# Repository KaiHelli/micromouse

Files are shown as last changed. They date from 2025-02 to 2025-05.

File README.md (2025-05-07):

# Micromouse

An autonomous micromouse designed and built at the Technical University of Munich (TUM) to explore and solve a 6×6 full-size maze and find its center. This project was done as part of the master practical course *Micromouse: Designing an Educational Racing-Robot from Scratch* under supervision of Dr. Alexander Lenz.

This mouse was built by the group of: Jázmin, Paulo, Ágnes, and Kai.

## Table of Contents

- [Micromouse](#micromouse)
  - [Table of Contents](#table-of-contents)
  - [Features](#features)
  - [Repository Structure](#repository-structure)
  - [Hardware Design](#hardware-design)
  - [Software Architecture](#software-architecture)

## Features

- **Hardware**  
  - dsPIC33FJ64MC804 microcontroller  
  - GP2Y0A51 analog distance sensors (front, left, right)  
  - ICM-20948 9-axis IMU for orientation
  - Toshiba TB6612FNG H-Bridge with Faulhaber DC motors  
  - 64×32 OLED display for real-time maze mapping  
  - RN4871 Bluetooth LE module & UART for data streaming  
  - Piezo buzzer (RTTTL melodies)  
  - 7.4 V battery input with 5 V/3.3 V linear regulators  
- **Firmware**  
  - UART & I²C drivers (sync/async)
  - OLED graphics library (SSD1306)
  - Timers & external interrupts with callback registration  
  - Odometry (encoders + gyro + distance sensors)  
  - Positional PD controller with feed-forward & side-wall PI  
  - Trapezoidal velocity profiles for straight & turning motions  
  - Flood-fill navigation with exploration & optimized final run  
- **Scripts**  
  - Python scripts for sensor calibration, feed-forward gain fitting, velocity profiling, and plotting  
  - Data analysis & visualization scripts and CSV data 

## Repository Structure

```
.
├── 3d/         # 3D-printed part designs (Autodesk Fusion) -> TODO: Add files
├── data/       # Raw & processed data logs
│ ├── *.csv
│ └── processed/
├── img/        # Figures/plots from experiments
├── imu_cal/    # IMU calibration scripts & data
├── logo/       # Team and TUM logos
├── pcb/        # Eagle files, design rule files & BOMs
├── scripts/    # Python tools for calibration & plotting
├── src/        # Embedded firmware source & build files
│ ├── adc.c/.h, i2c.c/.h, imu.c/.h, …
│ └── Makefile # Build configuration for MPLAB/xc16
└── README.md
```

## Hardware Design

1. **Schematic & PCB**  
   - Eagle files under `pcb/` (schematics, board, design rules, footprints).  
   - ADC decoupling / low-pass filter, star-shaped power rails, and IMU in center
2. **Sensors & Peripherals**  
   - Distance sensors: analog voltage → distance polynomial fit
   - IMU: offline accel/mag ellipsoid fit + gyro bias calibration on startup.  
   - OLED: SSD1306 over I²C for maze display.  
3. **Mechanical**  
   - Motor & sensor mounts (3D-printed; see `3d/`).  
   - Battery holder below PCB for low center of gravity.  

## Software Architecture

- **Configuration**
  - `src/constants.h`
  - `src/IOconfig.h/.c`
- **Drivers**  
  - `src/dma.c`, `src/clock.c`, `src/adc.c`, `src/uart.c`, `src/i2c.c`, `src/timers.c`, `src/pwm.c`, `src/switches.c`, `src/ssd1306.c`, …
- **Applications**  
  - `src/globalTimers.c` – provides a microsecond-resolution system timer running since power-up.  
  - `src/mazeSolver.c` – implements the flood-fill algorithm for exploration and the optimized run to the maze center.  
  - `src/oled.c` – manages the SSD1306 display’s frame buffer, draws the maze and updates only the regions that change.  
  - `src/rtttl.c` – decodes RTTTL ringtone strings and drives the piezo buzzer to play melodies.  
  - `src/imu.c` – interfaces with the 9-axis IMU over I²C, applies calibration, and reads gyro/accel/mag data.  
  - `src/sensor.s` – reads raw ADC values from the distance sensors and converts them into calibrated distance measurements.  
  - `src/motors.c` – controls the motor driver to set each wheel’s speed as a percentage of maximum.  
  - `src/motorEncoders.c` – reads quadrature encoder counts and uses a PLL to estimate wheel angular velocity.  
- **Control**  
  - `src/mouseController.c` – implements positional PD control with feed-forward terms for precise trajectory tracking  
  - `src/move.c` – generates trapezoidal velocity profiles for both linear and rotational movements  
- **Utilities**  
  - `src/data_visualizer/*.dvws` for creating interactive plots in MPLAB’s Data Visualizer  
- **Unused**
  - `src/odometry.c` – abandoned sensor-fusion odometry module, superseded by integrated controller-based estimation.

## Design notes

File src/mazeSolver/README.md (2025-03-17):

# Maze Traversal using Flood Fill
v1.0

## PID Control 
First implementation in demo project
```c
/*
 *         _
 *   /\/\ (_) ___ _ __ ___  _ __ ___   ___  _   _ ___  ___
 *  /    \| |/ __| '__/ _ \| '_ ` _ \ / _ \| | | / __|/ _ \
 * / /\/\ \ | (__| | | (_) | | | | | | (_) | |_| \__ \  __/
 * \/    \/_|\___|_|  \___/|_| |_| |_|\___/ \__,_|___/\___|
 *
 * Example program to showcase the Micromouse API for the demo mouse.
 *
 * File:   main.c
 *
 */

#include "UART.h"
#include "boot.h"
#include "configBits.h"
#include "encoders.h"
#include "globalTimer.h"
#include "leds.h"
#include "motors.h"
#include "sensors.h"
#include "switches.h"
#include "timers.h"

#include <stdio.h>
#include <xc.h>

/* EXAMPLE FUNCTIONS */

/**
 * Routine to toggle LED1 using a timer. This functions signature matches the TimerCallback typedef from the timers.h file.
 * @return 1 to keep the timer running, if 0 is returned the timer will stop
 */
int toggle_led1(void)
{
    LED1 = !LED1;
    return 1; // return 1 to keep the timer running
}

/**
 * Routine to toggle LED2 using the button SW1. This functions signature matches the SwitchCallback typedef from the switches.h file.
 * Returns nothing.
 */
void toggle_led2(void)
{
    LED2 = !LED2;
}

/**
 * Routine to toggle LED3 using the UART RX interrupt. This functions signature matches the UARTCallback typedef from the UART.h file.
 */
void toggle_led3(unsigned int registerContent)
{
    LED3 = !LED3;
}

/**
 * Routine to toggle LED4 using the UART TX interrupt. This functions signature matches the UARTCallback typedef from the UART.h file.
 */
void toggle_led4(unsigned int registerContent)
{
    LED4 = !LED4;
}

/**
 * Routine to stream sensor readings over UART. This can be used to visualize the sensor readings in MPLAB Data Visualizer.
 *
 * Workspace file "sensor_test.dvws" can be found in this directory to setup the correct variable streamer.
 *
 * See MPLAB X Visualizer documentation for the protocol: MPLABÂ® Data Visualizer User's Guide (DS50003001) - 5.2 Stream Format
 */
int stream_sensor_data(void)
{
    LED1 = !LED1;
    UART_TXint8(FRAME_MARKER); // start of visualizer frame
    UART_TXint8(sensors_readFront());
    UART_TXint8(sensors_readLeft());
    UART_TXint8(sensors_readRight());
    UART_TXUInt(sensors_readFrontRaw());
    UART_TXUInt(sensors_readLeftRaw());
    UART_TXUInt(sensors_readRightRaw());
    UART_TXLong(encoders_getAngleLeftDegrees());
    UART_TXLong(encoders_getAngleRightDegrees());
    UART_TXFloat(encoders_getAngleLeftRadians());
    UART_TXFloat(encoders_getAngleRightRadians());
    UART_TXFloat(encoders_getRPMLeft());
    UART_TXFloat(encoders_getRPMRight());
    UART_TXFloat(encoders_getRadPerSecLeft());
    UART_TXFloat(encoders_getRadPerSecRight());
    UART_TXLong(encoders_getTicksLeft());
    UART_TXLong(encoders_getTicksRight());
    UART_TXint8(~FRAME_MARKER); // end of visualizer frame (one's complement of start marker)
    return 1;                   // return 1 to keep the timer running
}

/* Prints the current time since boot in ms to UART, formatted in ASCII */
int transmit_time(void)
{
    char timestring[20];
    sprintf(timestring, "Time: %lu\n", globalTimer_getTimeInUS() / 1000); // devide by 1000 to convert to ms
    UART_TXString(timestring);
    return 1;
}

/**
 * Routine to toggle the motors using the button SW1. This functions signature matches the SwitchCallback typedef from the switches.h file.
 */
void toggle_motors(void)
{
    static int running = 0;
    if (running)
    {
        motors_setMotorLeft(0);
        motors_setMotorRight(0);
        running = 0;
    }
    else
    {
        motors_setMotorLeft(0.3);
        motors_setMotorRight(0.3);
        running = 1;
    }
}

struct PID{
    float K_p;
    float K_i;
    float K_d;
    float last_error;
    //output
    float w_l;
    float w_r;
    float w_f;
};

//PID struct
struct PID pid_state;

//state 
static int started = 0;

void init_PID(struct PID* pid) {
    pid->K_p = 0.0007;
    pid->K_i = 0;
    pid->K_d = 0.0001;
    pid->last_error = 0;
    pid->w_l = 0;
    pid->w_r = 0;
    pid->w_f = 0;
}

void update_PID(struct PID* pid, uint8_t left, uint8_t right, uint8_t front) {
    //TODO set w_f according to front distance
    float error = (float)(left - right);
    pid->w_l = pid->w_f - pid->K_p * error - pid->K_d * (error - pid->last_error);
    pid->w_r = pid->w_f + pid->K_p * error + pid->K_d * (error - pid->last_error);
    if(pid->w_l > 1) pid->w_l = 1.0;
    if(pid->w_r > 1) pid->w_r = 1.0;
    if(pid->w_l < -1) pid->w_l = -1.0;
    if(pid->w_r < -1) pid->w_r = -1.0;
    pid->last_error = error;
}

void toggle_control() {
    
    //initialize PID
    init_PID(&pid_state);
    
    if (started)
    {
        motors_setMotorLeft(0);
        motors_setMotorRight(0);
        started = 0;
    }
    else
    {   
        pid_state.w_f = 0.35;
        started = 1;
    } 
}

/* Prints the current time since boot in ms to UART, formatted in ASCII */
int update_control(void)
{   
    if (started) {
        uint8_t left = sensors_readLeft();
        uint8_t right = sensors_readRight();
        uint8_t front = sensors_readFront();
        update_PID(&pid_state, left, right, front);
        motors_setMotorLeft(pid_state.w_l);
        motors_setMotorRight(pid_state.w_r);
    }
    return 1;
}

/* MAIN FUNCTION */

int main() {
    
    LED1 = LEDOFF;
    LED2 = LEDOFF;
    LED3 = LEDOFF;
    LED4 = LEDOFF;

    // initializes the peripherals, must be called first
    boot_setup();

    // initializes the UART1 module with a baud rate of 115200
    UART_setup(115200);

    // Example timer usage
    timers_initTimerInMS(1, 419);
    timers_registerTimerCallback(1, &update_control);
    timers_startTimer(1);

    // test switches
    switches_registerSW1Callback(&toggle_control);

    // infinite loop
    while (1) {}
    return 0;
}

int main1()
{   
    //PID struct
    struct PID pid;
    
    LED1 = LEDOFF;
    LED2 = LEDOFF;
    LED3 = LEDOFF;
    LED4 = LEDOFF;

    // initializes the peripherals, must be called first
    boot_setup();

    // initializes the UART1 module with a baud rate of 115200
    UART_setup(115200);

    //initialize PID
    init_PID(&pid);
    
    // Example timer usage
    timers_initTimerInMS(1, 419);
    timers_registerTimerCallback(1, &transmit_time);
    timers_startTimer(1);

    // test switches
    switches_registerSW1Callback(&toggle_motors);

    // test UART callbacks
    UART_registerRX1Callback(&toggle_led3);
    UART_registerTX1Callback(&toggle_led4);

    // infinite loop
    while (1) {}
    return 0;
}
```

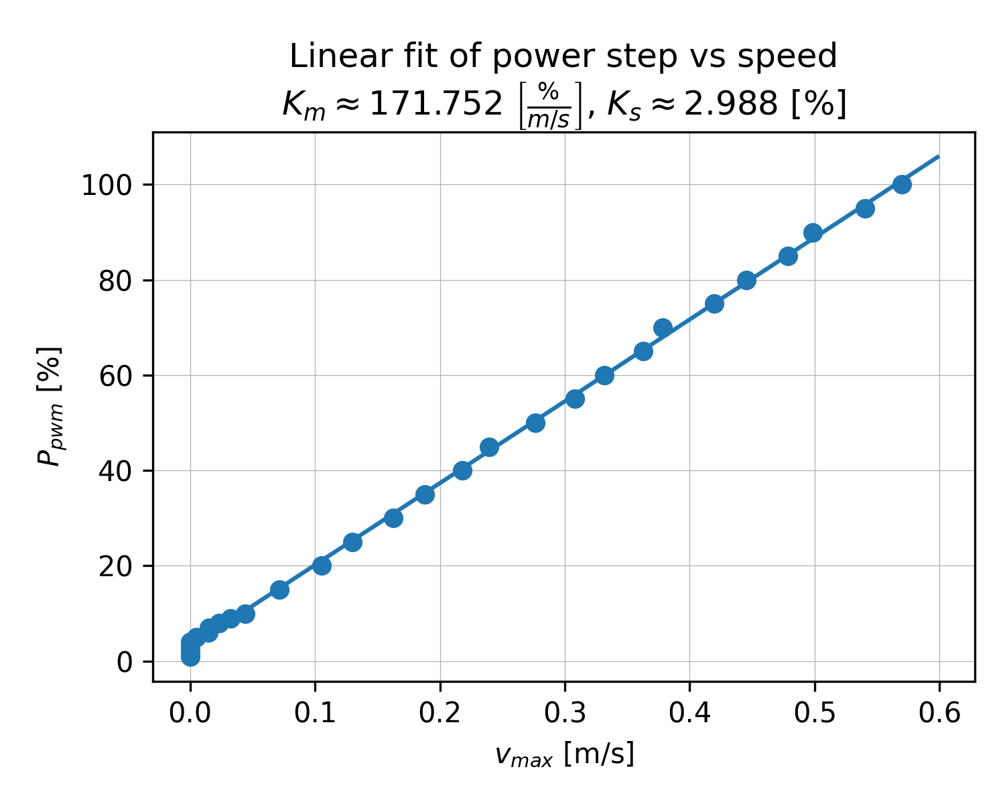
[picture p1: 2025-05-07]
img/vmax_fit_linear.png

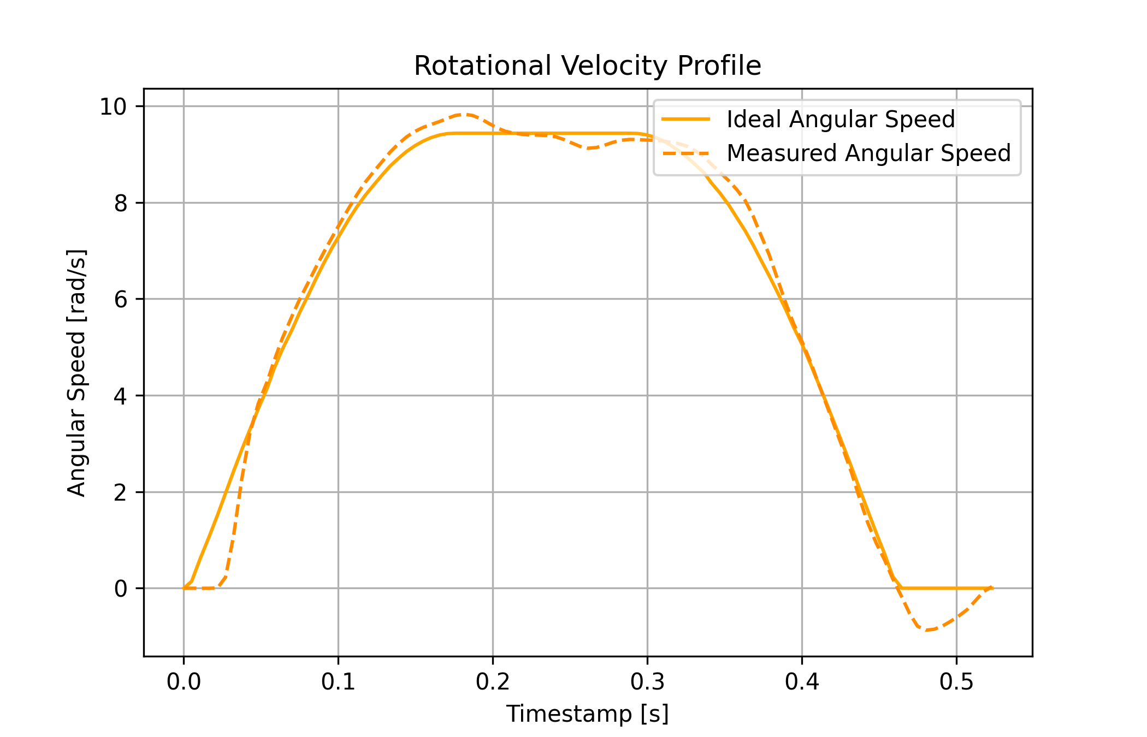
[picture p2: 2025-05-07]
img/vel_profile_angular.png

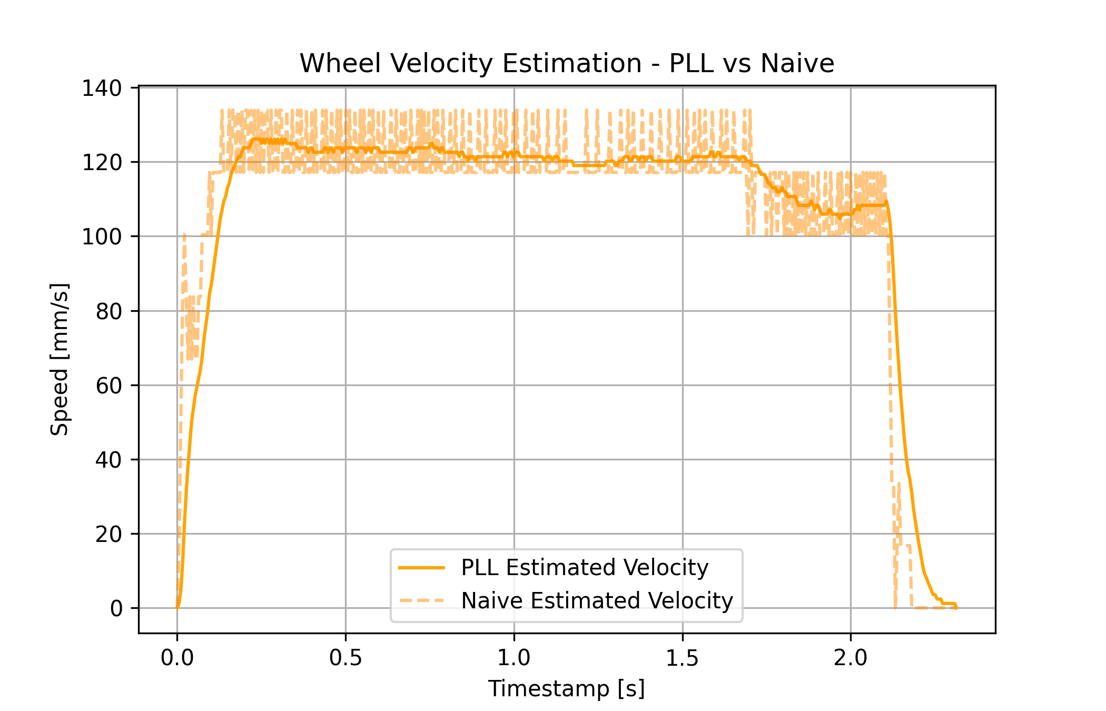
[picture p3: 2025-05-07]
img/enc_velocities_comparison.png

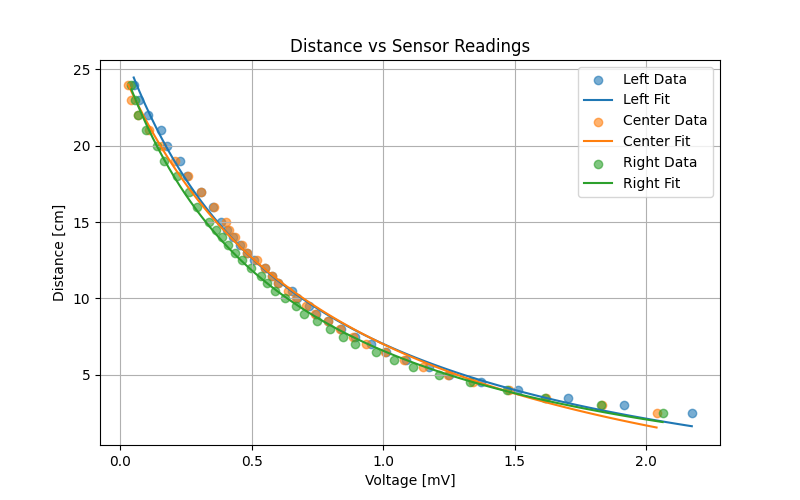
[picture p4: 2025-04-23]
img/distance_fast_sensor_fit.png

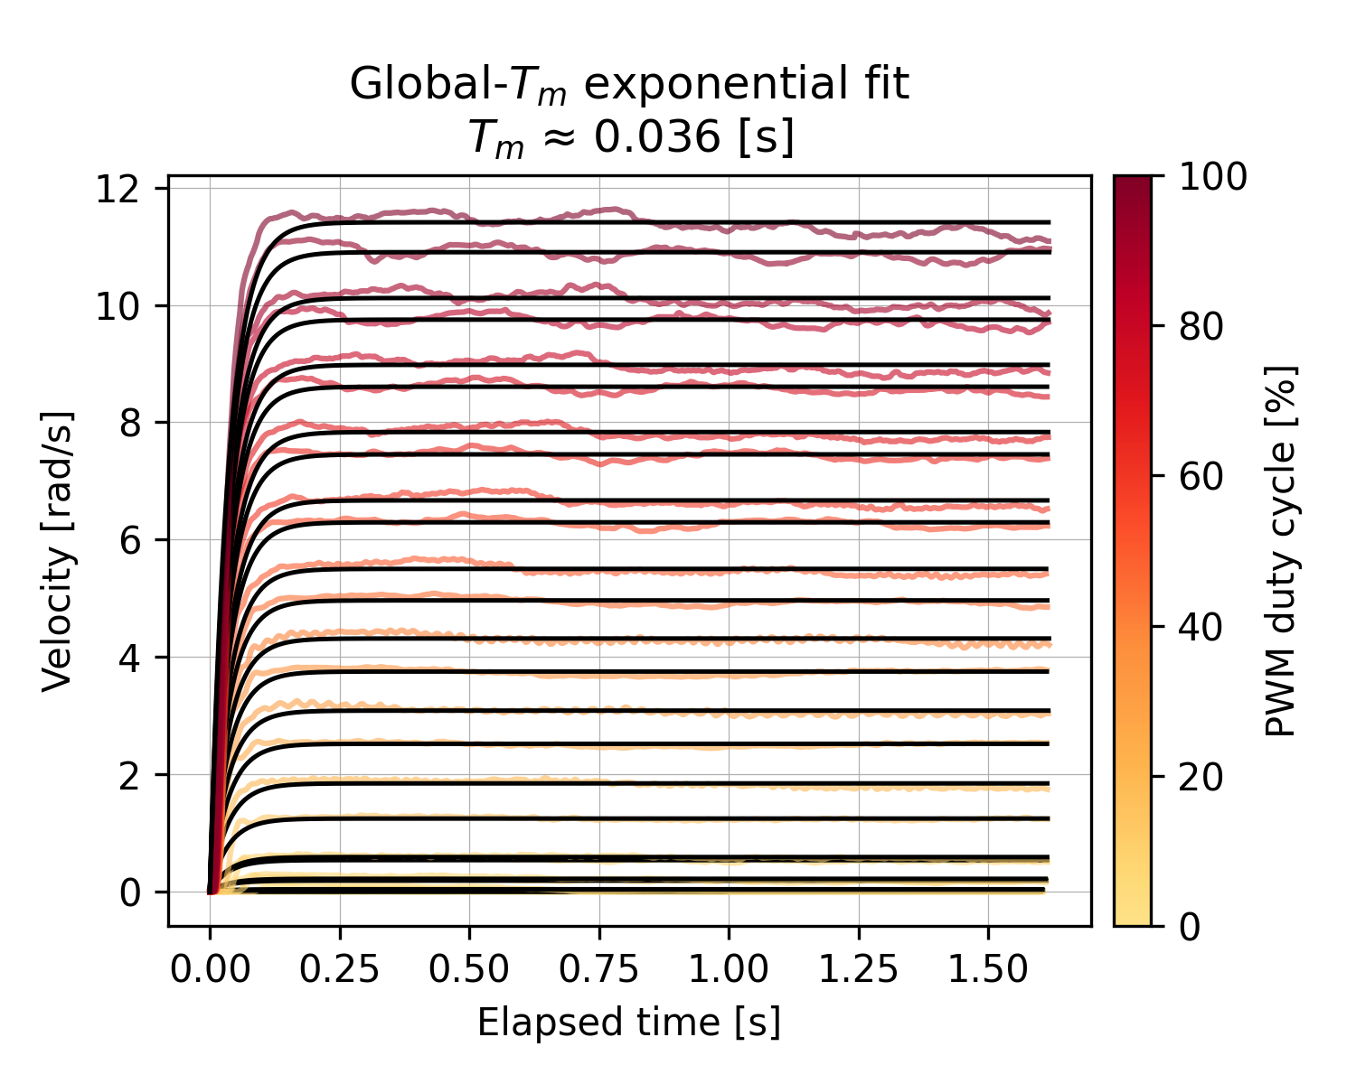
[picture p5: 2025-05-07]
img/Tm_fit_angular.png

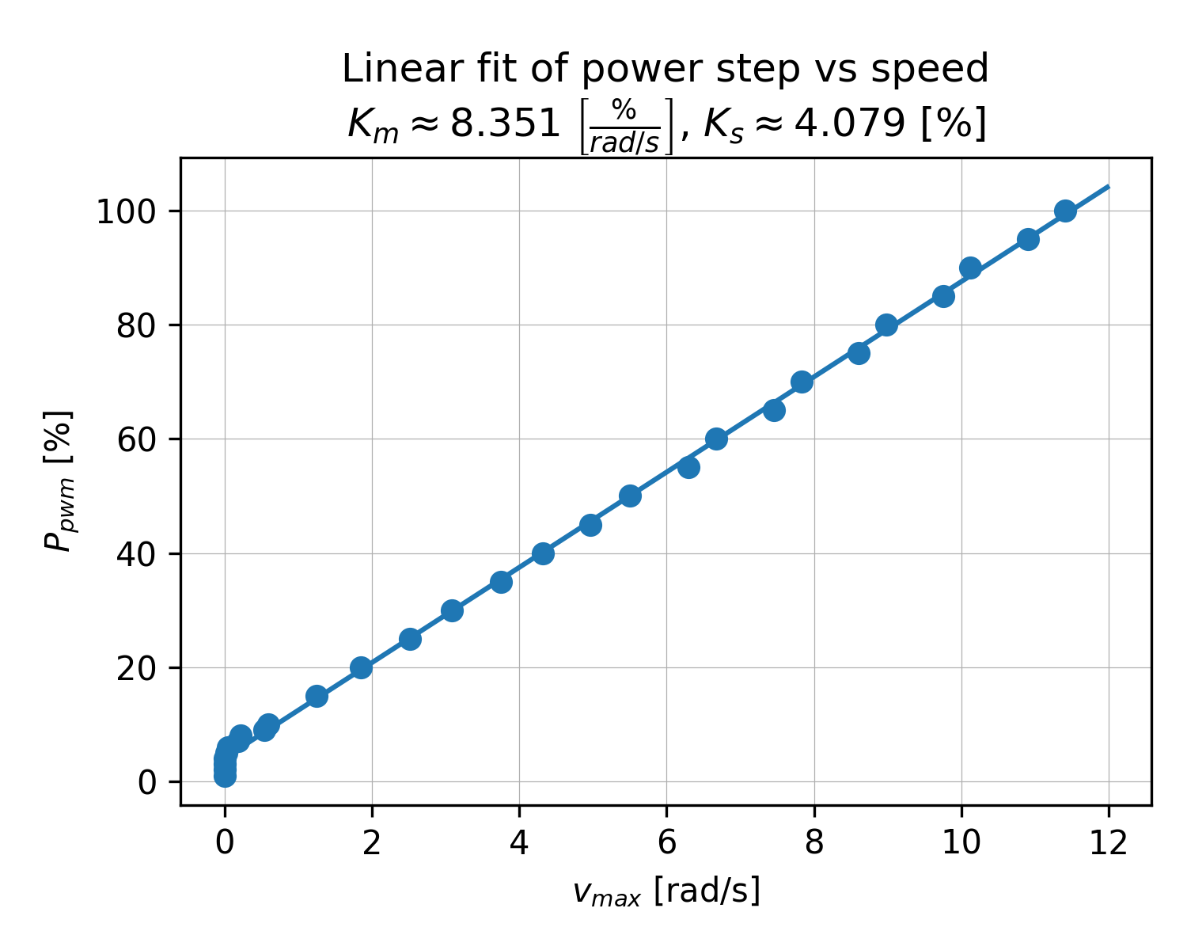
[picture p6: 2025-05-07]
img/vmax_fit_angular.png

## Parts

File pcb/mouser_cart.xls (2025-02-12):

WARENKORB
Dies ist keine Rechnung
11-Feb-25 18:27:51
 | Mouser-Nr. | Herst.- Nr. | Hersteller | Kunden-Teilenr | Beschreibung | RoHS | Lebenszyklus | Stückzahl | Preis (EUR) | Gesamtpreis: (EUR)
1 | 579-RN4871-I/RM140 | RN4871-I/RM140 | Microchip |  | Bluetooth-Module – 802.15.1 Bluetooth Low Energy BLE Module, Shielded, Antenna, ASCII Interface, 9x11.5mm | RoHS-konform |  | 1 | 8,78 € | 8,78 €
2 | 667-ERJ-PB6B1001V | ERJ-PB6B1001V | Panasonic |  | Dickfilmwiderstände - SMD 0805 Anti-Surge Res. 0.1%, 1Kohm | RoHS: Konform durch Ausnahmegenehmigung |  | 6 | 0,276 € | 1,66 €
3 | 771-PMEG4010ER115 | PMEG4010ER,115 | Nexperia |  | Schottky Dioden & Gleichrichter PMEG4010ER/SOD123W/SOD2 | RoHS: Konform durch Ausnahmegenehmigung |  | 1 | 0,20 € | 0,20 €
4 | 667-ERJ-PB6B2201V | ERJ-PB6B2201V | Panasonic |  | Dickfilmwiderstände - SMD 0805 Anti-Surge Res. 0.1%, 2.2Kohm | RoHS: Konform durch Ausnahmegenehmigung |  | 2 | 0,276 € | 0,55 €
5 | 667-ERJ-PB6B2701V | ERJ-PB6B2701V | Panasonic |  | Dickfilmwiderstände - SMD 0805 Anti-Surge Res. 0.1%, 2.7Kohm | RoHS: Konform durch Ausnahmegenehmigung |  | 1 | 0,323 € | 0,32 €
6 | 604-APT2012LZGCK | APT2012LZGCK | Kingbright |  | Einfarbige LEDs leds 2.0X1.2MM LOW CRNT | RoHS-konform |  | 3 | 0,513 € | 1,54 €
7 | 604-APT2012LVBCD | APT2012LVBC/D | Kingbright |  | Einfarbige LEDs leds 2.0X1.2MM LOW CRNT | RoHS-konform |  | 1 | 0,513 € | 0,51 €
8 | 604-APT2012LSECKJ3RV | APT2012LSECK/J3-PRV | Kingbright |  | Einfarbige LEDs leds 2.0X1.2MM LOW CRNT | RoHS-konform |  | 5 | 0,58 € | 2,90 €
9 | 179-TS046650BK100SMR | TS04-66-50-BK-100-SMT-TR | Same Sky |  | Sensorschalter 6 x 6 mm 5 mm Actuator Height 100 gf Black Surface Mount TR SPST Tactile | RoHS-konform | Neues Produkt | 2 | 0,181 € | 0,36 €
10 | 611-1101M2S3CQE2 | 1101M2S3CQE2 | C&K Switches |  | Schiebeschalter SP ON-NONE-ON PTH AG | RoHS-konform |  | 1 | 5,13 € | 5,13 €
11 | 151-302-RC | 151-302-RC | Kobiconn |  | Prüfstecker und Messbuchsen LONG YEL PCB TERM | RoHS-konform |  | 4 | 0,443 € | 1,77 €
12 | 571-1761681-1 | 1761681-1 | TE Connectivity |  | Sockel & Kabelgehäuse IDC LOW PRO HDR 6P VERT HT BLACK | RoHS-konform |  | 2 | 1,18 € | 2,36 €
13 | 81-LQH43PN470M26L | LQH43PN470M26L | Murata |  | Leistungsinduktivitäten – SMD 47 UH 20% | RoHS-konform |  | 1 | 0,466 € | 0,47 €
14 | 179-CPT-9019A-SMT-TR | CPT-9019A-SMT-TR | Same Sky |  | Lautsprecher u. Umformer 9.0 mm square 1.9 mm deep P 4.0 kHz 3 V SMT no driving circuit T&R package A | RoHS-konform | Neues Produkt | 1 | 0,836 € | 0,84 €
15 | 774-ATS16A-E | ATS16A-E | CTS |  | Quarze 16MHz 20pF 30ppm -40C 85C | RoHS-konform |  | 1 | 0,504 € | 0,50 €
16 | 485-4554 | 4554 | Adafruit |  | Entwicklungstools für multifunktionale Sensoren Adafruit TDK InvenSense ICM-20948 9-DoF IMU (MPU-9250 Upgrade) - STEMMA QT / Qwiic | RoHS-konform |  | 1 | 14,20 € | 14,20 €
17 | 852-GP2Y0A51SK0F | GP2Y0A51SK0F | Sharp Microelectronics |  | Entfernungssensor-Module - umschlossen | RoHS: Konform durch Ausnahmegenehmigung |  | 3 | 5,82 € | 17,46 €
18 | 757-TB6612FNGC8EL | TB6612FNG,C,8,EL | Toshiba |  | Motor / Bewegung / Zündungscontroller und Treiber Brush Motor Driver IC | RoHS-konform |  | 1 | 2,60 € | 2,60 €
19 | 926-LM1117DTX50NOPB | LM1117DTX-5.0/NOPB | Texas Instruments |  | LDO Spannungs-Regulator 800mA LDO Linear Reg A 926-LM1117DT50NOPB | RoHS-konform |  | 1 | 1,41 € | 1,41 €
20 | 926-LM1117DTX3.3NOPB | LM1117DTX-3.3/NOPB | Texas Instruments |  | LDO Spannungs-Regulator 800MA LDO LINEAR REG A 926-LM1117DT-3.3NOPB | RoHS-konform |  | 1 | 1,22 € | 1,22 €
21 | 579-DSPIC364MC804IPT | DSPIC33FJ64MC804-I/PT | Microchip |  | Digitale Signalprozessoren und Controller - DSP, DSC 16B DSC 64KB | RoHS-konform |  | 1 | 6,89 € | 6,89 €
22 | 667-ERJ-PB6B1002V | ERJ-PB6B1002V | Panasonic |  | Dickfilmwiderstände - SMD 0805 Anti-Surge Res. 0.1%, 10Kohm | RoHS: Konform durch Ausnahmegenehmigung |  | 4 | 0,276 € | 1,10 €
23 | 667-ERJ-PB6B5600V | ERJ-PB6B5600V | Panasonic |  | Dickfilmwiderstände - SMD 0805 Anti-Surge Res. 0.1%, 560ohm | RoHS: Konform durch Ausnahmegenehmigung |  | 2 | 0,257 € | 0,51 €
24 | 667-ERJ-PB6B1501V | ERJ-PB6B1501V | Panasonic |  | Dickfilmwiderstände - SMD 0805 Anti-Surge Res. 0.1%, 1.5Kohm | RoHS: Konform durch Ausnahmegenehmigung |  | 1 | 0,352 € | 0,35 €
25 | 710-61300211121 | 61300211121 | Wurth Elektronik |  | Sockel & Kabelgehäuse WR-PHD 2.54mm 2Pin T HT Header | RoHS-konform |  | 3 | 0,124 € | 0,37 €
26 | 710-61300311121 | 61300311121 | Wurth Elektronik |  | Sockel & Kabelgehäuse WR-PHD 2.54mm Hdr 3P Single Str Gold | RoHS-konform |  | 2 | 0,124 € | 0,25 €
27 | 710-61300411121 | 61300411121 | Wurth Elektronik |  | Sockel & Kabelgehäuse WR-PHD 2.54mm Hdr 4P Single Str Gold | RoHS-konform |  | 1 | 0,181 € | 0,18 €
28 | 710-61300611121 | 61300611121 | Wurth Elektronik |  | Sockel & Kabelgehäuse WR-PHD 2.54mm 6Pin T HT Header | RoHS-konform |  | 1 | 0,333 € | 0,33 €
29 | 710-61300411821 | 61300411821 | Wurth Elektronik |  | Sockel & Kabelgehäuse WR-PHD 2.54mm Scket Header 4 pins | RoHS-konform |  | 1 | 0,418 € | 0,42 €
30 | 710-61300611821 | 61300611821 | Wurth Elektronik |  | Sockel & Kabelgehäuse WR-PHD 2.54mm Socket Header 6 pins | RoHS-konform |  | 2 | 0,342 € | 0,68 €
31 | 710-61304011821 | 61304011821 | Wurth Elektronik |  | Platine-zu-Platine & Mezzanine-Steckverbinder WR-PHD 2.54 mm Socket Header 40P 1Row straight gold plating | RoHS-konform | Neu bei Mouser | 1 | 2,77 € | 2,77 €
32 | 710-61304011121 | 61304011121 | Wurth Elektronik |  | Sockel & Kabelgehäuse WR-PHD 2.54mm Hdr 40 P Single Str Gold | RoHS-konform |  | 1 | 1,45 € | 1,45 €
33 | 80-C0805C200J5GAUTO | C0805C200J5GACAUTO | KEMET |  | Kondensator aus mehreren Keramikschichten MLCC - SMD/SMT 50V 20pF C0G 0805 5% AEC-Q200 | RoHS-konform |  | 2 | 0,209 € | 0,42 €
34 | 80-C0805C104K4JAUTO | C0805C104K4JACAUTO | KEMET |  | Kondensator aus mehreren Keramikschichten MLCC - SMD/SMT Cap Cer 0805 0.1F 16VDC U2J | RoHS-konform |  | 8 | 0,57 € | 4,56 €
35 | 80-C0805C105J3RECAUT | C0805C105J3RECAUTO | KEMET |  | Kondensator aus mehreren Keramikschichten MLCC - SMD/SMT 25V 1uF X7R 0805 5% AEC-Q200 | RoHS-konform |  | 4 | 0,266 € | 1,06 €
36 | 80-C0805C106K4P | C0805C106K4PACTU | KEMET |  | Kondensator aus mehreren Keramikschichten MLCC - SMD/SMT 16V 10uF X5R 0805 10% | RoHS-konform |  | 6 | 0,162 € | 0,97 €
37 | 581-TAJP106K010RNJ | TAJP106K010RNJ | KYOCERA AVX |  | Tantalkondensatoren - fest für SMD 10V 10uF 10% | RoHS-konform |  | 3 | 0,542 € | 1,63 €
38 | 581-TLJR226M010R3800 | TLJR226M010R3800 | KYOCERA AVX |  | Tantalkondensatoren - fest für SMD 10V 22uF 20% ESR=380 0 | RoHS-konform |  | 2 | 0,656 € | 1,31 €
39 | 863-NTR1P02T1G | NTR1P02T1G | onsemi |  | MOSFETs -20V -1A P-Channel | RoHS-konform |  | 1 | 0,323 € | 0,32 €
Durch das Absenden Ihrer Bestellung erklären Sie sich mit diesen Geschäftsbedingungen einverstanden. (https://www.mouser.de/saleterms) |  |  |  |  |  |  |  |  | Ware: | 90,35 €
Die Preise sind zum angezeigten Datum und zur Uhrzeit reflektiert. |  |  |  |  |  |  |  |  | Versandkosten: | 0,00 €

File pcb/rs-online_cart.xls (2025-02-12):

RS Stock No | Quantity | Cost Centre | Description | Manufacturer Part. No. | Manufacturer name | Unit Price | Total Price
1805375 | 10 |  | RS PRO Stecker Leistungssteckverbinder, Stecker, 2P, Gold, 45A, 500 V dc | XT60PW-M | RS PRO | 1455 | 1455
2256195 | 1 |  | Midas 0.49Zoll OLED-Display 64 x 32pixels, 11.18 x 5.58mm Weiß Passiv-Matrix, I2C Interface | MDOB064032AV-WI | Midas | 673 | 673
8201649 | 20 |  | JST ZH Vorverdrahtete Crimp-Kontakte verzinnt 0.05mm², 300mm | 01SZHSZH-30L-300 | JST | 444 | 888
8201646 | 10 |  | JST ZH Steckverbindergehäuse Buchse 1.5mm, 3-polig / 1-reihig Gerade, Kabelmontage für Trennbarer Crimp-Steckverbinder | ZHR-3 | JST | 6 | 6

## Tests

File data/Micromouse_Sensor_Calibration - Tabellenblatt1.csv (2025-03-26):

Abstand [cm] | Left [/1000 V] | Center [/1000 V] | Right [/1000 V]
1 | 3170 | 3098 | 3107
1,5 | 2891 | 2662 | 2730
2 | 2481 | 2369 | 2354
2,5 | 2173 | 2039 | 2062
3 | 1917 | 1830 | 1828
3,5 | 1702 | 1617 | 1615
4 | 1514 | 1477 | 1472
4,5 | 1373 | 1342 | 1330
5 | 1252 | 1246 | 1213
5,5 | 1174 | 1151 | 1112
6 | 1085 | 1080 | 1042
6,5 | 1010 | 1008 | 971
7 | 952 | 934 | 894
7,5 | 892 | 886 | 846
8 | 840 | 836 | 797
8,5 | 792 | 789 | 749
9 | 744 | 742 | 700
9,5 | 719 | 707 | 670
10 | 671 | 670 | 626
10,5 | 652 | 639 | 589
11 | 602 | 602 | 560
11,5 | 578 | 576 | 537
12 | 552 | 551 | 498
12,5 | 510 | 522 | 463
13 | 484 | 481 | 437
13,5 | 455 | 463 | 412
14 | 430 | 438 | 388
14,5 | 406 | 413 | 364
15 | 382 | 403 | 338
16 | 354 | 357 | 293
17 | 307 | 309 | 264
18 | 255 | 259 | 216
19 | 229 | 208 | 166
20 | 180 | 158 | 139
21 | 155 | 111 | 100
22 | 106 | 67 | 70
23 | 71 | 42 | 56
24 | 52 | 31 | 43
25 | 36 | 23 | 33
30 | 22 | 23 | 22

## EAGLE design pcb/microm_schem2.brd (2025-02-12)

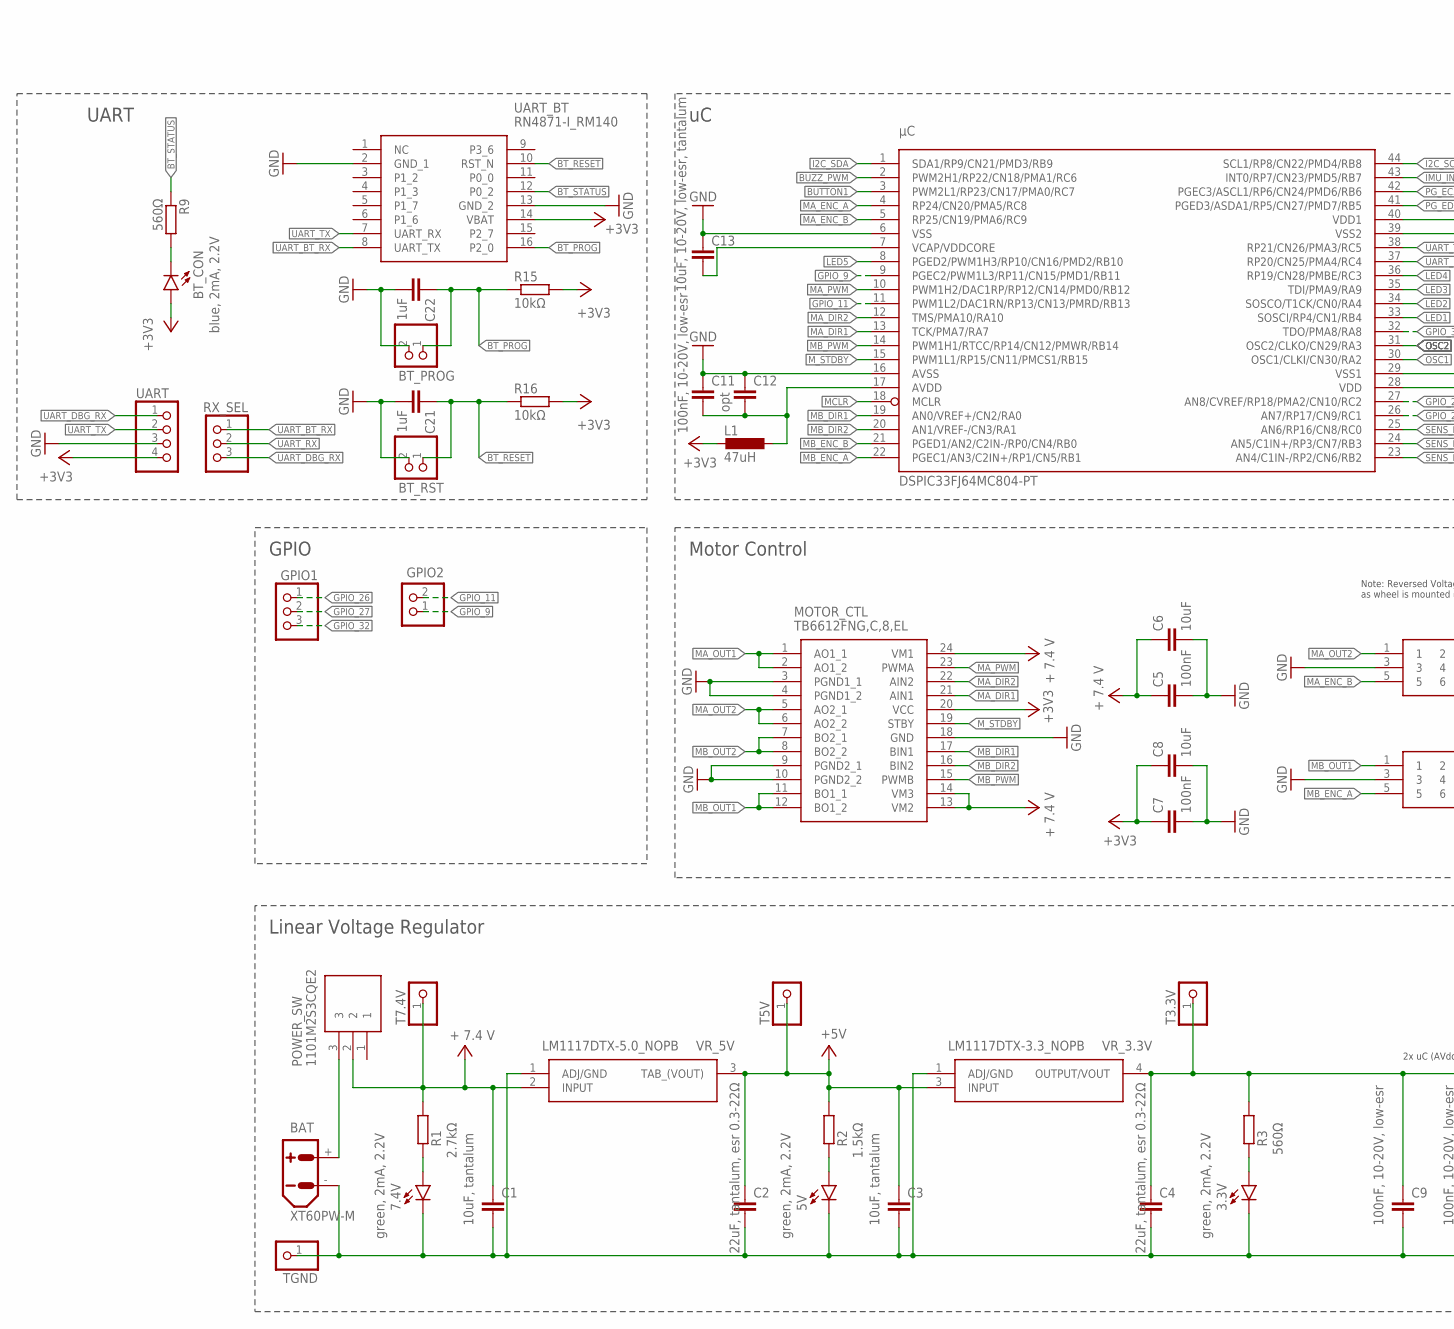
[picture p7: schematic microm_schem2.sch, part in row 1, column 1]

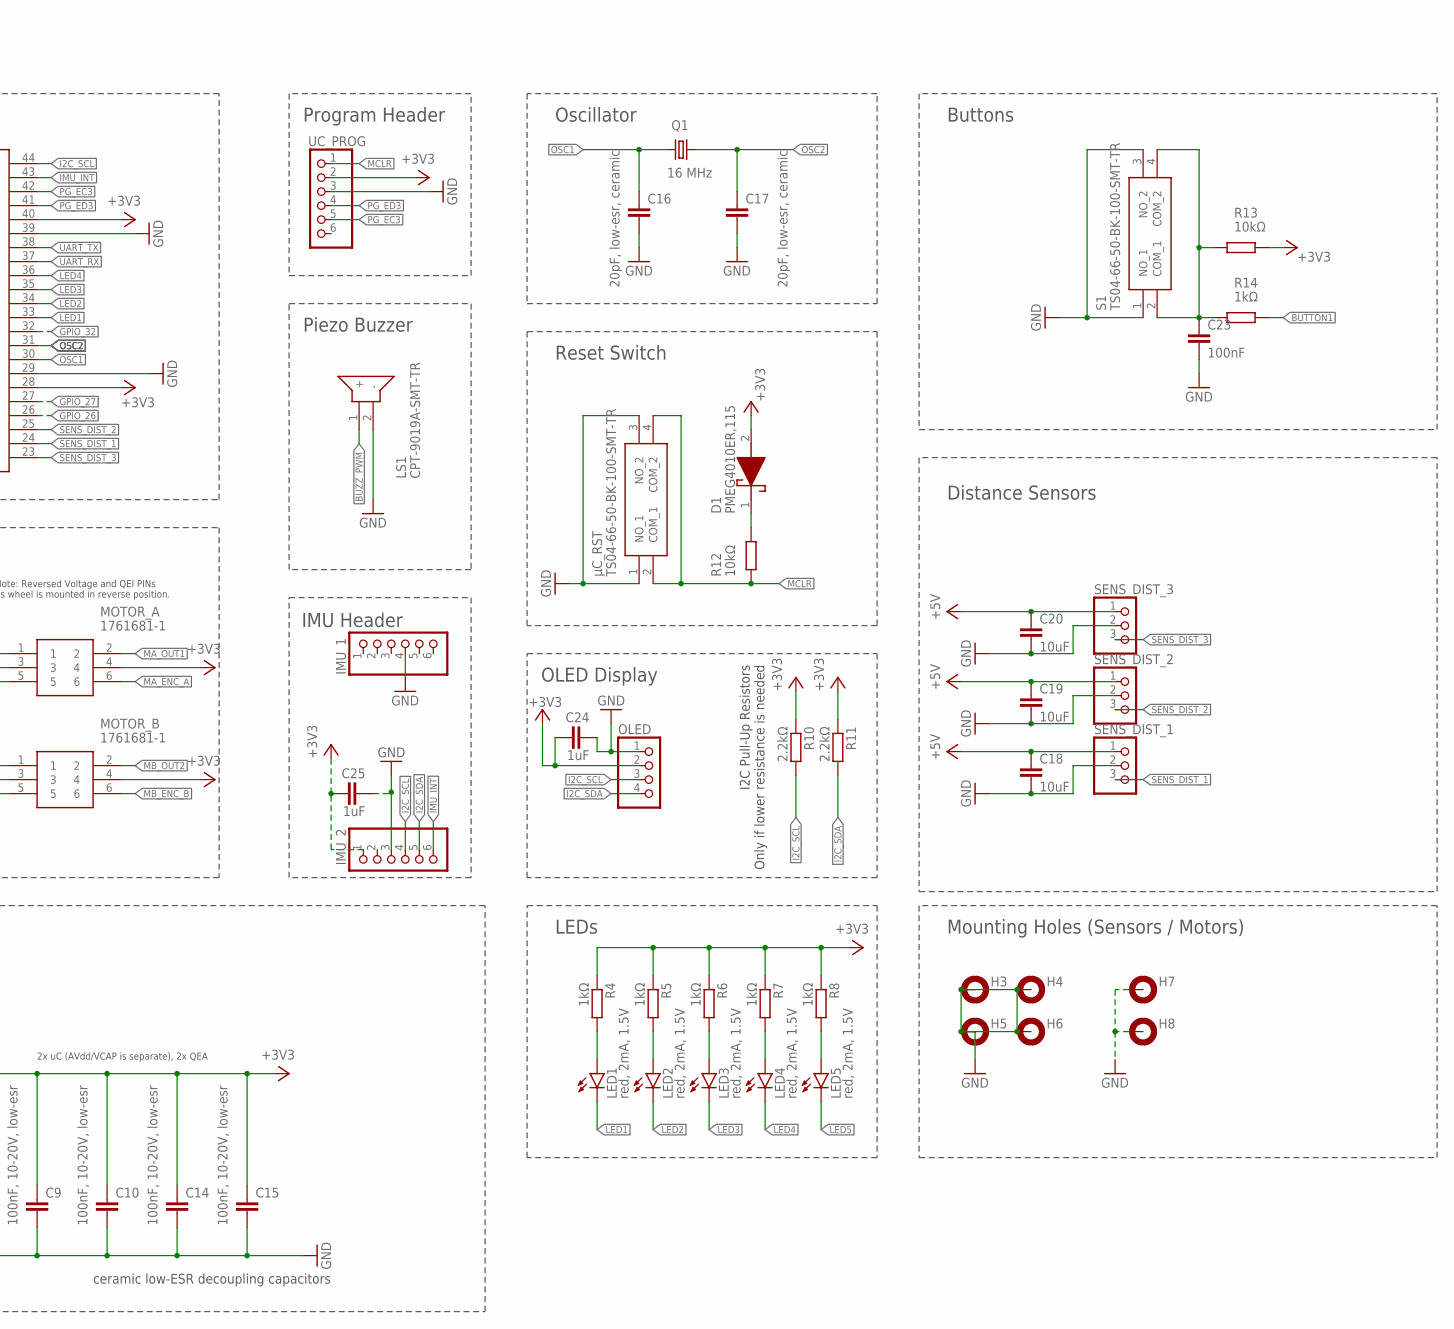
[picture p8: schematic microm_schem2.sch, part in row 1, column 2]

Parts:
3.3V, 5V, 7.4V: green, 2mA, 2.2V; CHIP-LED0805
BAT: XT60PW-M
BT_CON: blue, 2mA, 2.2V; CHIP-LED0805
BT_PROG: PINHD-1X2; 1X02
BT_RST: PINHD-1X2; 1X02
C1, C3: 10uF, tantalum; C0805
C2, C4: 22uF, tantalum, esr 0.3-22Ω; C0805
C5, C7, C23: 100nF; C0805
C6, C8, C18, C19, C20: 10uF; C0805
C9, C10, C11, C14, C15: 100nF, 10-20V, low-esr; C0805
C12: opt; C0805
C13: 10uF, 10-20V, low-esr, tantalum; C0805
C16, C17: 20pF, low-esr, ceramic; C0805
C21, C22, C24, C25: 1uF; C0805
D1: PMEG4010ER,115; PMEG4010ER115
GPIO1: PINHD-1X3; 1X03
GPIO2: PINHD-1X2; 1X02
H3, H4, H5, H6, H7, H8: MOUNT-PAD-ROUND2.8; 2,8-PAD
IMU_1, IMU_2: PINHD-1X6; 1X06
L1: 47uH; L1812
LED1, LED2, LED3, LED4, LED5: red, 2mA, 1.5V; CHIPLED_0805
LS1: CPT-9019A-SMT-TR; CPT9019ASMTTR
MOTOR_A: 1761681-1; SHDR6W67P254_2X3_1524X916X922P
MOTOR_B: 1761681-1; SHDR6W67P254_2X3_1524X916X922P
MOTOR_CTL: TB6612FNG,C,8,EL; SOP65P760X160-24N
OLED: PINHD-1X4; 1X04
POWER_SW: 1101M2S3CQE2; 1000-SERIES(SPDT)
Q1: 16 MHz; HC49/S
R1: 2.7kΩ; R0805
R2: 1.5kΩ; R0805
R3, R9: 560Ω; R0805
R4, R5, R6, R7, R8, R14: 1kΩ; R0805
R10, R11: 2.2kΩ; R0805
R12, R13, R15, R16: 10kΩ; R0805
RX_SEL: PINHD-1X3; 1X03
S1: TS04-66-50-BK-100-SMT-TR; TS046650BK100SMTTR
SENS_DIST_1, SENS_DIST_2, SENS_DIST_3: PINHD-1X3; 1X03
T3.3V, T5V, T7.4V: PINHD-1X1; 1X01
TGND: PINHD-1X1; 1X01
UART: PINHD-1X4; 1X04
UART_BT: RN4871-I_RM140; RN4871IRM140
UC_PROG: PINHD-1X6; 1X06
VR_3.3V: LM1117DTX-3.3_NOPB; LM1117DTX33NOPB
VR_5V: LM1117DTX-5.0_NOPB; LM78M05CDT
µC_RST: TS04-66-50-BK-100-SMT-TR; TS046650BK100SMTTR
μC: DSPIC33FJ64MC804-PT; TQFP44

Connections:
+3V3: BT_CON.A, C4.1, C7.1, C8.1, C9.1, C10.1, C14.1, C15.1, C24.1, C25.1, D1.2 (A), IMU_2.1, L1.2, MOTOR_A.4, MOTOR_B.4, MOTOR_CTL.20 (VCC), OLED.2, R3.1, R4.1, R5.1, R6.1, R7.1, R8.1, R10.1, R11.1, R13.2, R15.2, R16.2, T3.3V.1, UART.4, UART_BT.14 (VBAT), UC_PROG.2, VR_3.3V.4 (OUTPUT/VOUT), μC.28 (VDD), μC.40 (VDD1)
+5V: C2.1, C3.1, C18.1, C19.1, C20.1, R2.1, SENS_DIST_1.1, SENS_DIST_2.1, SENS_DIST_3.1, T5V.1, VR_3.3V.3 (INPUT), VR_5V.3 (TAB_(VOUT))
+7V4: C1.1, C5.1, C6.1, MOTOR_CTL.13 (VM2), MOTOR_CTL.14 (VM3), MOTOR_CTL.24 (VM1), POWER_SW.2, R1.1, T7.4V.1, VR_5V.2 (INPUT)
BT_PROG: BT_PROG.1, C22.1, R15.1, UART_BT.16 (P2_0)
BT_RESET: BT_RST.1, C21.1, R16.1, UART_BT.10 (RST_N)
BT_STATUS: R9.1, UART_BT.12 (P0_2)
BUTTON1: R14.2, μC.3 (PWM2L1/RP23/CN17/PMA0/RC7)
BUZZ_PWM: LS1.1 (+), μC.2 (PWM2H1/RP22/CN18/PMA1/RC6)
GND: 3.3V.C, 5V.C, 7.4V.C, BAT.-, BT_PROG.2, BT_RST.2, C1.2, C2.2, C3.2, C4.2, C5.2, C6.2, C7.2, C8.2, C9.2, C10.2, C11.1, C12.1, C13.1, C14.2, C15.2, C16.2, C17.2, C18.2, C19.2, C20.2, C21.2, C22.2, C23.2, C24.2, C25.2, H3.B2,8, H4.B2,8, H5.B2,8, H6.B2,8, H7.B2,8, H8.B2,8, IMU_1.4, IMU_2.3, LS1.2 (-), MOTOR_A.3, MOTOR_B.3, MOTOR_CTL.3 (PGND1_1), MOTOR_CTL.4 (PGND1_2), MOTOR_CTL.9 (PGND2_1), MOTOR_CTL.10 (PGND2_2), MOTOR_CTL.18 (GND), OLED.1, S1.1 (NO_1), S1.3 (NO_2), SENS_DIST_1.2, SENS_DIST_2.2, SENS_DIST_3.2, TGND.1, UART.3, UART_BT.2 (GND_1), UART_BT.13 (GND_2), UC_PROG.3, VR_3.3V.1 (ADJ/GND), VR_5V.1 (ADJ/GND), µC_RST.1 (NO_1), µC_RST.3 (NO_2), μC.6 (VSS), μC.16 (AVSS), μC.29 (VSS1), μC.39 (VSS2)
GPIO_9: GPIO2.1, μC.9 (PGEC2/PWM1L3/RP11/CN15/PMD1/RB11)
GPIO_11: GPIO2.2, μC.11 (PWM1L2/DAC1RN/RP13/CN13/PMRD/RB13)
GPIO_26: GPIO1.1, μC.26 (AN7/RP17/CN9/RC1)
GPIO_27: GPIO1.2, μC.27 (AN8/CVREF/RP18/PMA2/CN10/RC2)
GPIO_32: GPIO1.3, μC.32 (TDO/PMA8/RA8)
I2C_SCL: IMU_2.4, OLED.3, R10.2, μC.44 (SCL1/RP8/CN22/PMD4/RB8)
I2C_SDA: IMU_2.5, OLED.4, R11.2, μC.1 (SDA1/RP9/CN21/PMD3/RB9)
IMU_INT: IMU_2.6, μC.43 (INT0/RP7/CN23/PMD5/RB7)
LED1: LED1.C, μC.33 (SOSCI/RP4/CN1/RB4)
LED2: LED2.C, μC.34 (SOSCO/T1CK/CN0/RA4)
LED3: LED3.C, μC.35 (TDI/PMA9/RA9)
LED4: LED4.C, μC.36 (RP19/CN28/PMBE/RC3)
LED5: LED5.C, μC.8 (PGED2/PWM1H3/RP10/CN16/PMD2/RB10)
MA_DIR1: MOTOR_CTL.21 (AIN1), μC.13 (TCK/PMA7/RA7)
MA_DIR2: MOTOR_CTL.22 (AIN2), μC.12 (TMS/PMA10/RA10)
MA_ENC_A: MOTOR_A.6, μC.4 (RP24/CN20/PMA5/RC8)
MA_ENC_B: MOTOR_A.5, μC.5 (RP25/CN19/PMA6/RC9)
MA_OUT1: MOTOR_A.2, MOTOR_CTL.1 (AO1_1), MOTOR_CTL.2 (AO1_2)
MA_OUT2: MOTOR_A.1, MOTOR_CTL.5 (AO2_1), MOTOR_CTL.6 (AO2_2)
MA_PWM: MOTOR_CTL.23 (PWMA), μC.10 (PWM1H2/DAC1RP/RP12/CN14/PMD0/RB12)
MB_DIR1: MOTOR_CTL.17 (BIN1), μC.19 (AN0/VREF+/CN2/RA0)
MB_DIR2: MOTOR_CTL.16 (BIN2), μC.20 (AN1/VREF-/CN3/RA1)
MB_ENC_A: MOTOR_B.5, μC.22 (PGEC1/AN3/C2IN+/RP1/CN5/RB1)
MB_ENC_B: MOTOR_B.6, μC.21 (PGED1/AN2/C2IN-/RP0/CN4/RB0)
MB_OUT1: MOTOR_B.1, MOTOR_CTL.11 (BO1_1), MOTOR_CTL.12 (BO1_2)
MB_OUT2: MOTOR_B.2, MOTOR_CTL.7 (BO2_1), MOTOR_CTL.8 (BO2_2)
MB_PWM: MOTOR_CTL.15 (PWMB), μC.14 (PWM1H1/RTCC/RP14/CN12/PMWR/RB14)
MCLR: R12.1, UC_PROG.1, µC_RST.2 (COM_1), µC_RST.4 (COM_2), μC.18 (MCLR)
M_STDBY: MOTOR_CTL.19 (STBY), μC.15 (PWM1L1/RP15/CN11/PMCS1/RB15)
unnamed: BT_CON.C, R9.2
unnamed: BAT.+, POWER_SW.3
unnamed: LED1.A, R4.2
unnamed: 7.4V.A, R1.2
unnamed: C11.2, C12.2, L1.1, μC.17 (AVDD)
unnamed: C23.1, R13.1, R14.1, S1.2 (COM_1), S1.4 (COM_2)
unnamed: D1.1 (K), R12.2
unnamed: LED2.A, R5.2
unnamed: 5V.A, R2.2
unnamed: 3.3V.A, R3.2
unnamed: LED3.A, R6.2
unnamed: LED4.A, R7.2
unnamed: LED5.A, R8.2
OSC1: C16.1, Q1.1, μC.30 (OSC1/CLKI/CN30/RA2)
OSC2: C17.1, Q1.2, μC.31 (OSC2/CLKO/CN29/RA3)
PG_EC3: UC_PROG.5, μC.42 (PGEC3/ASCL1/RP6/CN24/PMD6/RB6)
PG_ED3: UC_PROG.4, μC.41 (PGED3/ASDA1/RP5/CN27/PMD7/RB5)
SENS_DIST_1: SENS_DIST_1.3, μC.24 (AN5/C1IN+/RP3/CN7/RB3)
SENS_DIST_2: SENS_DIST_2.3, μC.25 (AN6/RP16/CN8/RC0)
SENS_DIST_3: SENS_DIST_3.3, μC.23 (AN4/C1IN-/RP2/CN6/RB2)
UART_BT_RX: RX_SEL.1, UART_BT.8 (UART_TX)
UART_DBG_RX: RX_SEL.3, UART.1
UART_RX: RX_SEL.2, μC.37 (RP20/CN25/PMA4/RC4)
UART_TX: UART.2, UART_BT.7 (UART_RX), μC.38 (RP21/CN26/PMA3/RC5)
VCAP/VDDCORE: C13.2, μC.7 (VCAP/VDDCORE)

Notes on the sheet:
Oscillator
Program Header
Reset Switch
Distance Sensors
Motor Control
ceramic low-ESR decoupling capacitors
Linear Voltage Regulator
LEDs
Buttons
Piezo Buzzer
IMU Header
UART
2x uC (AVdd/VCAP is separate), 2x QEA
Note: Reversed Voltage and QEI PINs as wheel is mounted in reverse position.
I2C Pull-Up Resistors Only if lower resistance is needed
Mounting Holes (Sensors / Motors)
OLED Display
GPIO

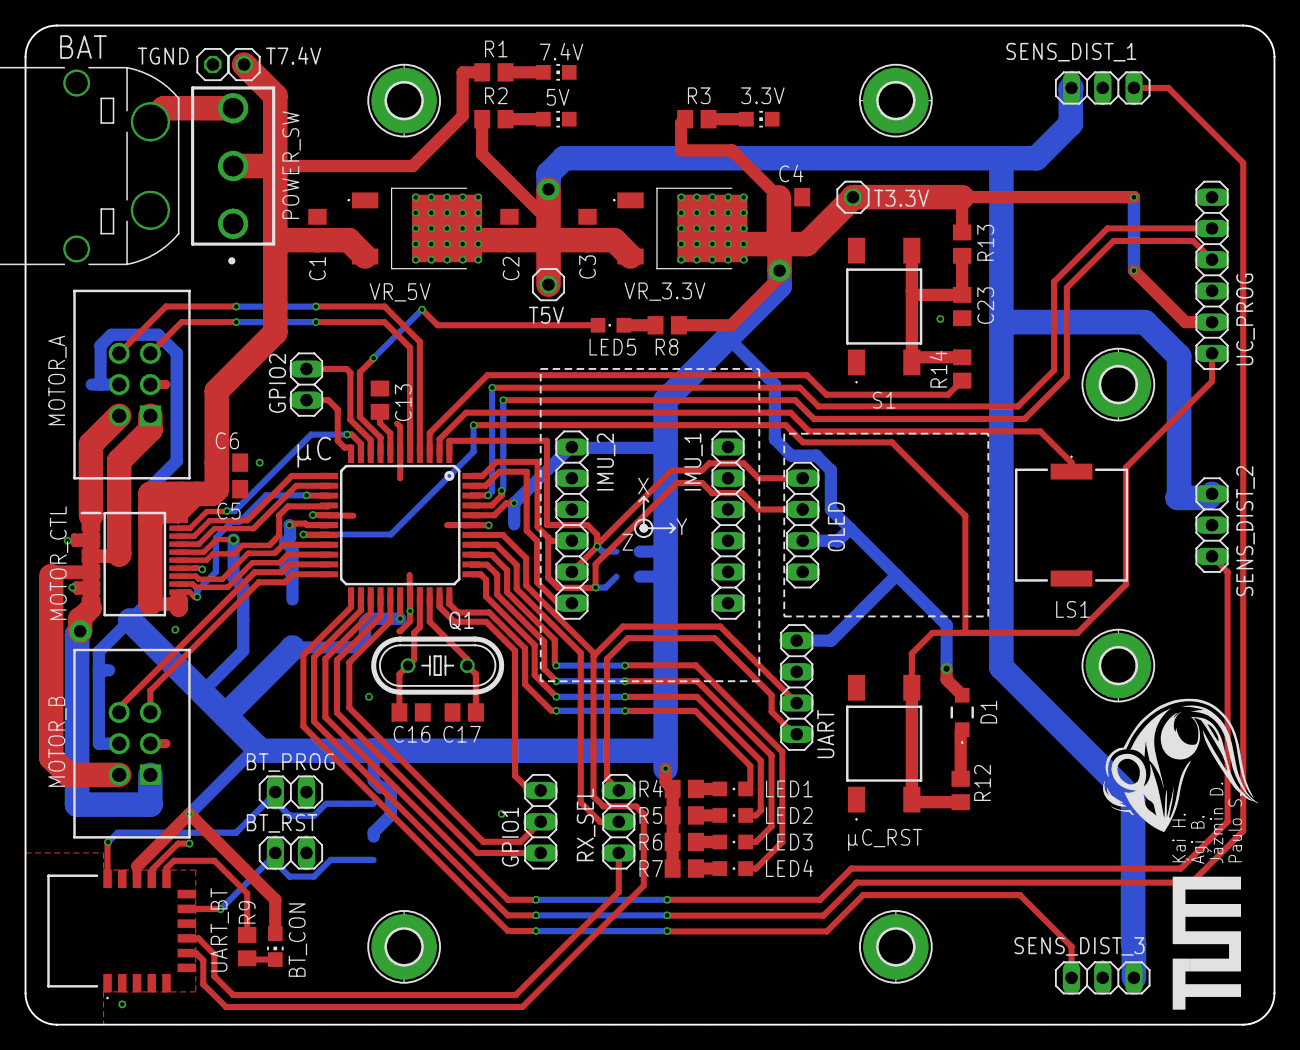
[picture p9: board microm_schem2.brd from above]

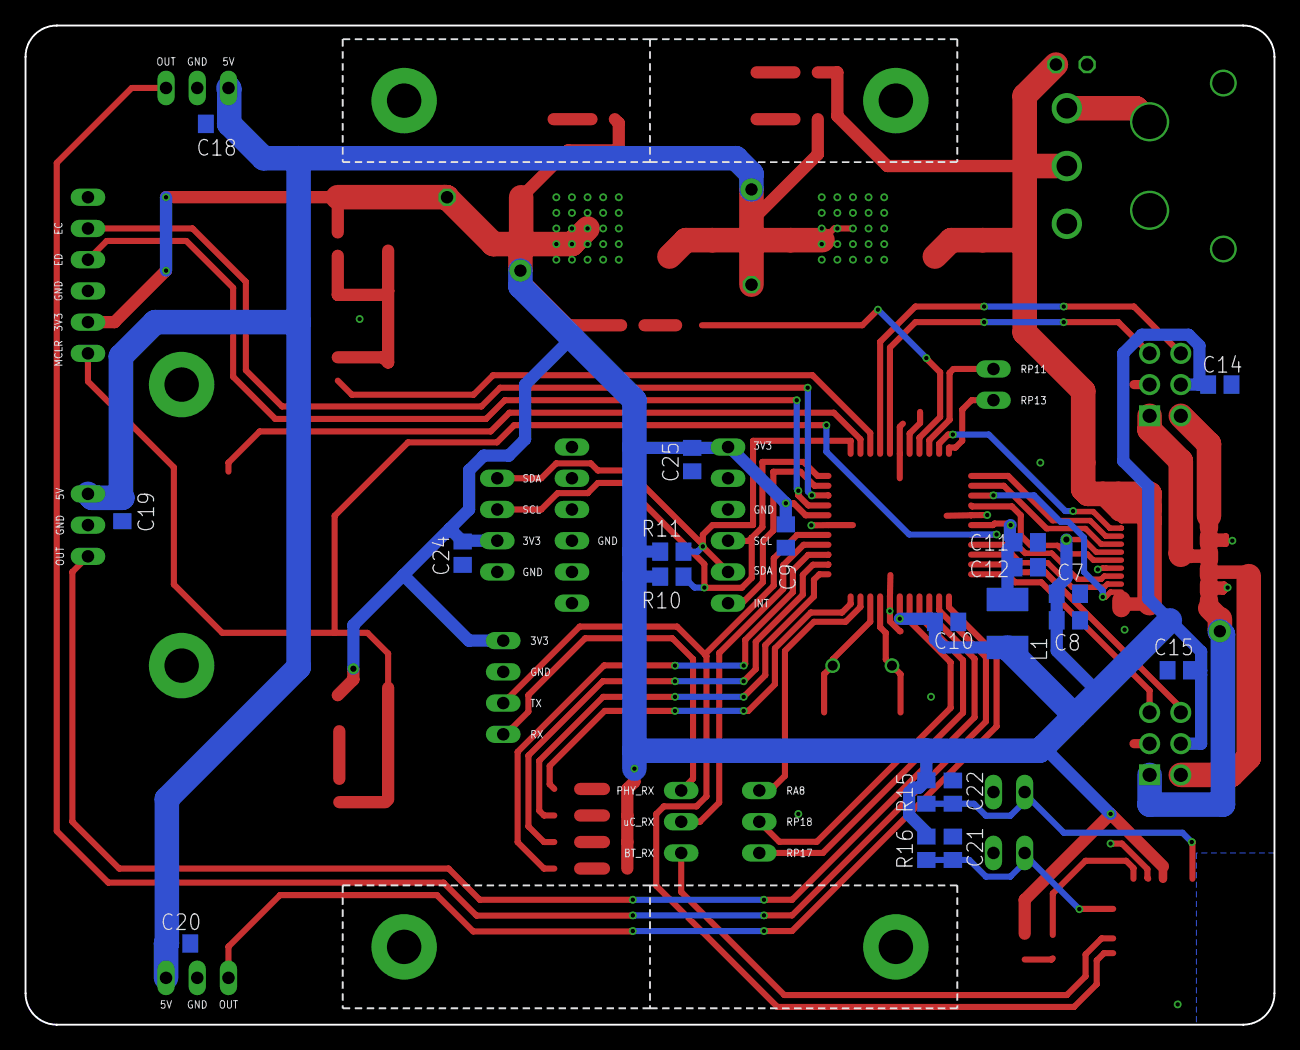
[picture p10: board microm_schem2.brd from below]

Board: 2 copper layers, 101.6 x 81.3 mm, 88 parts (20 on the bottom side), 63 nets.

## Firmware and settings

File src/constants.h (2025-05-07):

#ifndef CONSTANTS_H
#define CONSTANTS_H

#include <math.h>

/* Universal constants */

#define MICROSECONDS_PER_MILLISECOND   1000UL
#define MICROSECONDS_PER_SECOND        1000000UL
#define MILLISECONDS_PER_SECOND        1000UL               

#define MICROMETERS_PER_MILLIMETER     1000UL
#define MILLIMETERS_PER_METER          1000UL
#define MICROMETERS_PER_METER          1000000UL

#define RAD2DEG      (180.0f / (float)M_PI)
#define DEG2RAD      ((float)M_PI / 180.0f)

/* Maze geometry (ISO 18 cm cell) */

#define CELL_DIMENSION_MM            180.0f
#define WALL_WIDTH_MM                12.2f
#define CELL_DIAGONAL_MM             ((sqrtf(2.0f) * CELL_DIMENSION_MM) / 2.0f)
#define MIDDLE_MAZE_DISTANCE_MM      ((CELL_DIMENSION_MM - WALL_WIDTH_MM) / 2.0f)

/* Pre-computed micrometre versions */
#define CELL_DIMENSION_UM            ((int32_t)(CELL_DIMENSION_MM  * MICROMETERS_PER_MILLIMETER))
#define WALL_WIDTH_UM                ((int32_t)(WALL_WIDTH_MM      * MICROMETERS_PER_MILLIMETER))
#define CELL_DIAGONAL_UM             ((int32_t)(CELL_DIAGONAL_MM   * MICROMETERS_PER_MILLIMETER))
#define MIDDLE_MAZE_DISTANCE_UM      ((int32_t)(MIDDLE_MAZE_DISTANCE_MM * MICROMETERS_PER_MILLIMETER))

/* Mouse physical layout */
#define MOUSE_MOTOR_TAIL_MM          50.8f
#define MOUSE_MOTOR_HEAD_MM          50.922f
#define MOUSE_AXIS_SEPARATION_MM     0.0f

#define MOUSE_LENGTH_MM              (MOUSE_MOTOR_TAIL_MM + MOUSE_MOTOR_HEAD_MM)
#define MOUSE_TAIL_MM                (MOUSE_MOTOR_TAIL_MM + MOUSE_AXIS_SEPARATION_MM / 2.0f)
#define MOUSE_HEAD_MM                (MOUSE_LENGTH_MM - MOUSE_TAIL_MM)
#define MOUSE_START_SHIFT_MM         (MOUSE_TAIL_MM + WALL_WIDTH_MM / 2.0f)

/* Drive-wheel parameters */

#define MOUSE_WHEEL_SEPARATION_MM       97.55f
#define MOUSE_WHEEL_RADIUS_BIAS_MM      0.0f       // TODO: bias needed to match odometry with reality
#define MOUSE_WHEEL_RADIUS_MM           (30.0f + MOUSE_WHEEL_RADIUS_BIAS_MM)
#define MOUSE_WHEEL_DIAMETER_MM         (2.0f * MOUSE_WHEEL_RADIUS_MM)
#define MOUSE_WHEEL_CIRCUMFERENCE_MM    (MOUSE_WHEEL_DIAMETER_MM * (float) M_PI)

/* Physics / motor capability */

#define MOUSE_MASS_KG                   0.307f
#define MOUSE_MOMENT_OF_INERTIA_KGM2    0.0005641125f   // \frac{0.307}{12}\cdot \left(0.105^2+0.105^2\right)

/* Motor data sheet (33:1 HP + 30 mm wheel) */
#define MOUSE_WHEEL_MAX_ACC_DPS2        3000.0f // dps2 -- exact 3054.976
#define MOUSE_WHEEL_MAX_VEL_DPS         878.65 // dps  -- exact 1022.728 - but takes longer to reach from 878.65 on
#define MOUSE_WHEEL_MAX_VEL_MMPS        (MOUSE_WHEEL_MAX_VEL_DPS * DEG2RAD * MOUSE_WHEEL_RADIUS_MM)

#define MOUSE_MAX_ANGULAR_VELOCITY_RADPS ((2.0f * MOUSE_WHEEL_RADIUS_MM * (MOUSE_WHEEL_MAX_VEL_DPS * DEG2RAD)) / MOUSE_WHEEL_SEPARATION_MM)

#define MOUSE_WHEEL_TORQUE_CONT_NM      0.03f
#define MOUSE_WHEEL_TORQUE_PEAK_NM      0.10f

/*  F = tau / r - keep everything in metres here */
#define MOUSE_WHEEL_MAX_FORCE_CONT_N \
        (MOUSE_WHEEL_TORQUE_CONT_NM / (MOUSE_WHEEL_RADIUS_MM / (float)MILLIMETERS_PER_METER))
#define MOUSE_WHEEL_MAX_FORCE_PEAK_N \
        (MOUSE_WHEEL_TORQUE_PEAK_NM / (MOUSE_WHEEL_RADIUS_MM / (float)MILLIMETERS_PER_METER))

/* Encoder constants */

#define ENC_TICKS_PER_REV            (4U * 16U * 33U)          /* 4×QEI × 16 slots × 33:1 */
#define ENC_TICKS_TO_RAD             (2.0f * (float)M_PI / (float)ENC_TICKS_PER_REV)
#define ENC_TICKS_TO_DEG             (360.0f / (float) ENC_TICKS_PER_REV)
#define ENC_DIST_PER_TICK_MM         (MOUSE_WHEEL_CIRCUMFERENCE_MM / (float) ENC_TICKS_PER_REV)
#define ENC_DIST_PER_TICK_UM         (ENC_DIST_PER_TICK_MM * MICROMETERS_PER_MILLIMETER)

/* Control & alignment tolerances */

#define KEEP_FRONT_DISTANCE_TOLERANCE_MM   1
#define KEEP_FRONT_DISTANCE_TOLERANCE_UM   ((int32_t) (KEEP_FRONT_DISTANCE_TOLERANCE_MM * MICROMETERS_PER_MILLIMETER))

#define CORRECT_FRONT_DISTANCE_BIAS_MM     -10
#define CORRECT_FRONT_DISTANCE_BIAS_UM     ((int32_t) CORRECT_FRONT_DISTANCE_BIAS_MM * MICROMETERS_PER_MILLIMETER)

#define SHIFT_AFTER_180_DEG_TURN_MM        5.0f
#define SHIFT_AFTER_180_DEG_TURN_UM        ((int32_t) (SHIFT_AFTER_180_DEG_TURN_MM * MICROMETERS_PER_MILLIMETER))

#define SHIFT_DISTANCE_MM                  10
#define SHIFT_DISTANCE_UM                  ((int32_t) (SHIFT_DISTANCE_MM * MICROMETERS_PER_MILLIMETER))

#endif /* CONSTANTS_H */

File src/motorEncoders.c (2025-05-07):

/* Source code inspired by:
 *
 * Encoder Velocity PLL State Estimator: Odrive Robotics
 * - https://discourse.odriverobotics.com/t/rotor-encoder-pll-and-velocity/224
 * - https://github.com/odriverobotics/ODrive/blob/master/Firmware/MotorControl/encoder.cpp
 */ 

#include <xc.h>
#include <math.h>
#include <stdint.h>
#include <stdbool.h>

#include "atomic.h"
#include "constants.h"
#include "interrupts.h"
#include "IOconfig.h"
#include "motorEncoders.h"
#include "uart.h"
#include "globalTimers.h"
#include "fastPID.h"

// Global variables for the rotation counts.
// QEI1 is used for the left encoder and QEI2 for the right encoder.
volatile int32_t rotationCount1; // QEI1 (ENCODER_LEFT)
volatile int32_t rotationCount2; // QEI2 (ENCODER_RIGHT)

//--------------------------------------------------------------------------
// Global volatile variables holding the most recent velocity estimates.
// We assume the enumeration for MotorEncoder_t maps ENCODER_LEFT -> 0
// and ENCODER_RIGHT -> 1.
//--------------------------------------------------------------------------
volatile float encoderPosEst[2]         = { 0.0f, 0.0f };
volatile float encoderVelEst[2]         = { 0.0f, 0.0f };

//volatile float currentVelocityDegPerSec[2] = {0.0f, 0.0f};
volatile float currentVelocityRadPerSec[2] = {0.0f, 0.0f};
volatile float currentVelocityMmPerSec[2] = {0.0f, 0.0f};

// Global storage for last encoder positions and the time at which they
// were last updated. These are used only by the timer-driven update.
volatile uint64_t lastVelocityUpdateTime = 0;

volatile bool encVelInit = false;

// PI gains
#define ENC_PLL_KP  2.0f * 50.0f
#define ENC_PLL_KI  (0.25f * ENC_PLL_KP * ENC_PLL_KP)

#define ENC_MIN_VEL 0.001f
/*-------------------------------------------------------------------------
  Utility Function: readEncoderCount
  Atomically reads the encoder count by combining the hardware position counter 
  with the software-maintained rotation counter.
-------------------------------------------------------------------------*/
static inline int32_t readEncoderCount(MotorEncoder_t encoder)
{
    int32_t count;
    
    uint16_t state = _atomic_enter();
    
    switch(encoder)
    {
        case ENCODER_LEFT:
            count = rotationCount1 + POSCNT;
            break;
        case ENCODER_RIGHT:
            count = rotationCount2 + POS2CNT;
            break;
        default:
            count = 0;
            break;
    }
    
    _atomic_leave(state);
    
    return count;
}

void initMotorEncoders() {
    initQEI(ENCODER_LEFT, 0);
    initQEI(ENCODER_RIGHT, 0);
}

/*-------------------------------------------------------------------------
  Function: initQEI
  Initializes either QEI1 (for ENCODER_RIGHT) or QEI2 (for ENCODER_LEFT) 
  based on the encoder parameter.
-------------------------------------------------------------------------*/
void initQEI(MotorEncoder_t encoder, uint16_t startPos)
{
    switch(encoder)
    {
        case ENCODER_LEFT:
            QEI1CONbits.QEISIDL = 1;         // Disable module in idle mode
            QEI1CONbits.QEIM = 0b111;        // 4x mode with reset by match
            QEI1CONbits.SWPAB = 1;           // Swap Phase A and B
            QEI1CONbits.PCDOUT = 0;          // disable position counter direction pin 
            QEI1CONbits.TQGATE = 0;          // timer gated time acc disabled
            QEI1CONbits.POSRES = 0;          // index does not reset position counter
            QEI1CONbits.TQCS = 0;            // internal clock source (Tcy))
            QEI1CONbits.UPDN_SRC = 0;        // direction of position counter determined using internal logic
            
            MAXCNT = 0xffff;
            POSCNT = startPos;
            rotationCount1 = 0;
            
            IFS3bits.QEI1IF = 0;             // clear interrupt flag 
            IEC3bits.QEI1IE = 1;             // enable interrupt
            IPC14bits.QEI1IP = IP_QEI;
            break;
        case ENCODER_RIGHT:
            QEI2CONbits.QEISIDL = 1;         // Disable module in idle mode
            QEI2CONbits.QEIM = 0b111;        // 4x mode with reset by match
            QEI2CONbits.SWPAB = 1;           // Swap Phase A and B
            QEI2CONbits.PCDOUT = 0;          // disable position counter direction pin 
            QEI2CONbits.TQGATE = 0;          // timer gated time acc disabled
            QEI2CONbits.POSRES = 0;          // index does not reset position counter
            QEI2CONbits.TQCS = 0;            // internal clock source (Tcy))
            QEI2CONbits.UPDN_SRC = 0;        // direction of position counter determined using internal logic
            
            MAX2CNT = 0xffff;
            POS2CNT = startPos;
            rotationCount2 = 0;
            
            IFS4bits.QEI2IF = 0;             // clear interrupt flag 
            IEC4bits.QEI2IE = 1;             // enable interrupt
            IPC18bits.QEI2IP = IP_QEI;
            break;
        default:
            break;
    }
}

/*-------------------------------------------------------------------------
  Interrupt Service Routines for QEI roll-over/under detection
-------------------------------------------------------------------------*/
void __attribute__((__interrupt__, auto_psv)) _QEI1Interrupt(void)
{
    IFS3bits.QEI1IF = 0; 
    if (POSCNT < 32768) {
        rotationCount1 += ENC_MAX_VALUE;  // Positive roll-over
    } else {
        rotationCount1 -= ENC_MAX_VALUE;  // Negative roll-over
    }
}

void __attribute__((__interrupt__, auto_psv)) _QEI2Interrupt(void)
{
    IFS4bits.QEI2IF = 0; 
    if (POS2CNT < 32768) {
        rotationCount2 += ENC_MAX_VALUE;  // Positive roll-over
    } else {
        rotationCount2 -= ENC_MAX_VALUE;  // Negative roll-over
    }
}

/*-------------------------------------------------------------------------
  Function: getPositionInCounts
  Returns the current encoder position (including any rotation adjustments).
-------------------------------------------------------------------------*/
int32_t getEncoderPositionCounts(MotorEncoder_t encoder)
{
    return readEncoderCount(encoder);
}

/*-------------------------------------------------------------------------
  Function: getPositionInRad
  Converts the encoder count into a position in radians.
-------------------------------------------------------------------------*/
float getEncoderPositionRad(MotorEncoder_t encoder)
{
    int32_t currentEncoderPosition = readEncoderCount(encoder);
    return currentEncoderPosition * ENC_TICKS_TO_RAD;
}

/*-------------------------------------------------------------------------
  Function: getPositionInRad
  Converts the encoder count into a position in degrees.
-------------------------------------------------------------------------*/
float getEncoderPositionDeg(MotorEncoder_t encoder)
{
    int32_t currentEncoderPosition = readEncoderCount(encoder);
    return currentEncoderPosition * ENC_TICKS_TO_DEG;
}
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

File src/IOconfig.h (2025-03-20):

#ifndef IOCONFIG_H
#define IOCONFIG_H

#define SW1 !PORTCbits.RC7
#define IMU_INT PORTBbits.RB7

#define MA_DIR1 LATAbits.LATA7
#define MA_DIR2 LATAbits.LATA10
#define MB_DIR1 LATAbits.LATA0
#define MB_DIR2 LATAbits.LATA1

#define MA_PWM_MODULE  1
#define MA_PWM_CHANNEL 2

#define MB_PWM_MODULE  1
#define MB_PWM_CHANNEL 1

#define LED5_PWM_MODULE  1
#define LED5_PWM_CHANNEL 3

#define BUZZ_PWM_MODULE  2
#define BUZZ_PWM_CHANNEL 1

#define M_STDBY LATBbits.LATB15

#define LED1 LATBbits.LATB4
#define LED2 LATAbits.LATA4
#define LED3 LATAbits.LATA9
#define LED4 LATCbits.LATC3
#define LED5 LATBbits.LATB10

#define GPIO09 LATBbits.LATB11
#define GPIO11 LATBbits.LATB12
#define GPIO26 LATCbits.LATC1
#define GPIO27 LATCbits.LATC2
#define GPIO32 LATAbits.LATA8

#define LEDON 0
#define LEDOFF 1

/**
 * @brief Configures all necessary I/O pins and directions.
 * 
 * Sets up the digital/analog configuration for the device pins, and any
 * additional I/O initialization that may be required.
 * NOTE: ADC and PWM setup is done in adc.c and pwm.c
 */
void setupIO();

#endif /* IOCONFIG_H */

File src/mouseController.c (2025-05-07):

/* Source code inspired by:
 *
 * Feedforward Gains: Peter Harrison - mazerunner-core / motorlab
 * - https://github.com/ukmars/mazerunner-core/tree/main/mazerunner-core
 * - https://github.com/ukmars/motorlab/blob/main/documents/dirty-pd-controller.pdf
 * Control Loops and Kinematics: Bulebule
 * - https://github.com/Bulebots/bulebule
 * - https://github.com/Bulebots/mmlib
 */ 

#include "mouseController.h"
#include "fastPID.h"
#include "motorEncoders.h"
#include "motors.h"
#include "uart.h"
#include "sensors.h"
#include "globalTimers.h"
#include "move.h"
#include "constants.h"
#include "imu.h"
#include "odometry.h"
#include "atomic.h"

#include "clock.h" // Has to be imported before libpic30, as it defines FCY
#include <libpic30.h>

#include <stdio.h>
#include <stdint.h>
#include <math.h>
#include <stdlib.h>
#include <stdbool.h>
#include <string.h>

#define SIDE_WALL_DETECTION         ((uint32_t) (CELL_DIMENSION_UM * 0.90))
#define FRONT_WALL_DETECTION        ((uint32_t) (CELL_DIMENSION_UM * 0.90))
#define FAR_FRONT_WALL_DETECTION    ((uint32_t) (CELL_DIMENSION_UM * 1.50))

/*
#define MCTRL_LIN_PID_KP                8.0f
#define MCTRL_LIN_PID_KD                16.0f
#define MCTRL_ANG_PID_KP                0.05f
#define MCTRL_ANG_PID_KD                1.0f
#define MCTRL_ANG_SENS_PID_KP           2.0f
#define MCTRL_ANG_SENS_PID_KI           4.0f
*/

#define FEEDFORWARD_CTRL
#ifdef FEEDFORWARD_CTRL

#define MCTRL_LIN_FF_TM                 (0.07839f)          // forward time constant (initially 0.07839)
#define MCTRL_LIN_FF_KM                 (1.0f / 171.752f)   // (m/s) / pwm %
#define MCTRL_LIN_FF_KS                 (2.988f)

#define MCTRL_ANG_FF_TM                 (0.03573f)         // forward time constant (initially 0.03573f)
#define MCTRL_ANG_FF_KM                 (1.0f / 8.351f)    // (rad/s) / pwm %
#define MCTRL_ANG_FF_KS                 (4.079f)

#define MCTRL_LIN_FF_ZETA               (0.707f)
#define MCTRL_LIN_FF_TD                 (MCTRL_LIN_FF_TM)

#define MCTRL_ANG_FF_ZETA               (0.707f)
#define MCTRL_ANG_FF_TD                 (MCTRL_ANG_FF_TM)

//#define MCTRL_LIN_PID_KP                (16.0f * MCTRL_LIN_FF_TM / (MCTRL_LIN_FF_KM * MCTRL_LIN_FF_ZETA * MCTRL_LIN_FF_ZETA * MCTRL_LIN_FF_TD * MCTRL_LIN_FF_TD))
//#define MCTRL_LIN_PID_KD                ((8.0f * MCTRL_LIN_FF_TM - MCTRL_LIN_FF_TD) / (MCTRL_LIN_FF_KM * MCTRL_LIN_FF_TD))
//#define MCTRL_ANG_PID_KP                (16.0f * MCTRL_ANG_FF_TM / (MCTRL_ANG_FF_KM * MCTRL_ANG_FF_ZETA * MCTRL_ANG_FF_ZETA * MCTRL_ANG_FF_TD * MCTRL_ANG_FF_TD))
//#define MCTRL_ANG_PID_KD                ((8.0f * MCTRL_ANG_FF_TM - MCTRL_ANG_FF_TD) / (MCTRL_ANG_FF_KM * MCTRL_ANG_FF_TD))

#define MCTRL_LIN_PID_KP                (2.376771f)
#define MCTRL_LIN_PID_KD                (0.040756f)
#define MCTRL_ANG_PID_KP                (0.5f)
#define MCTRL_ANG_PID_KD                (0.015f)
#define MCTRL_ANG_SENS_PID_KP           (10.0f)
#define MCTRL_ANG_SENS_PID_KI           (0.0f)

typedef struct {
    float Ks;       // static bias               (PWM%)
    float Kv;       // speed gain                (PWM% * s / m   or   PWM% � s / rad)
    float Ka;       // acceleration gain         (PWM% * s^2 / m  or   PWM% � s^2 / rad)
    float prev_v;   // previous target speed     (m/s or rad/s)
} FFProfile_t;

static FFProfile_t ffLin = {
    .Ks = MCTRL_LIN_FF_KS,
    .Kv = 1.0f / MCTRL_LIN_FF_KM,
    .Ka = MCTRL_LIN_FF_TM / MCTRL_LIN_FF_KM,
    .prev_v = 0.0f
};

static FFProfile_t ffAng = {
    .Ks = MCTRL_ANG_FF_KS,
    .Kv = 1.0f / MCTRL_ANG_FF_KM,
    .Ka = MCTRL_ANG_FF_TM / MCTRL_ANG_FF_KM,
    .prev_v = 0.0f
};

#else

#define MCTRL_LIN_PID_KP                (42.0f)
#define MCTRL_LIN_PID_KD                (0.10666f)
#define MCTRL_ANG_PID_KP                (1.6f)
#define MCTRL_ANG_PID_KD                (0.006933f)
#define MCTRL_ANG_SENS_PID_KP           (2.0f)
#define MCTRL_ANG_SENS_PID_KI           (4.0f)

#endif


typedef struct {
    float Kp;
    float Ki;
    float Kd;
} PIDGains_t;

static volatile PIDGains_t pidLin;
static volatile PIDGains_t pidAng;
static volatile PIDGains_t pidAngSens;

static volatile float maxForce = MOUSE_WHEEL_MAX_FORCE_CONT_N;
static volatile float maxLinearSpeed = MOUSE_WHEEL_MAX_VEL_MMPS / MILLIMETERS_PER_METER;

static volatile float pidFrequency = 0.0f;

static volatile float targetLinearSpeed = 0.0f;
static volatile float idealLinearSpeed = 0.0f;
static volatile float idealAngularSpeed = 0.0f;

static volatile float linearError = 0.0f;
static volatile float angularError = 0.0f;
static volatile float lastLinearError = 0.0f;
static volatile float lastAngularError = 0.0f;

static volatile bool collisionDetected = false;
static volatile bool mouseControlEnabled = false;
static volatile bool sideSensorsCloseControlEnabled = false;
static volatile bool sideSensorsFarControlEnabled = false;

static volatile float sideSensorsIntegral;

float getMaxForce(void)
{
	return atomic_read_f32(&maxForce);
}

void setMaxForce(float value)
{
    atomic_write_f32(&maxForce, value);
}

void resetMaxForce(void)
{
    atomic_write_f32(&maxForce, MOUSE_WHEEL_MAX_FORCE_CONT_N);
}

float getLinearAcceleration(void)
{
	return 2 * getMaxForce() / MOUSE_MASS_KG;
}

float getLinearDeceleration(void)
{
	return 2 * getMaxForce() / MOUSE_MASS_KG;
}

float getTargetLinearSpeed(void)
{
	return atomic_read_f32(&targetLinearSpeed);
}

void setTargetLinearSpeed(float value)
{
    atomic_write_f32(&targetLinearSpeed, value);
}

float getIdealLinearSpeed(void)
{
	return atomic_read_f32(&idealLinearSpeed);
}

void setIdealLinearSpeed(float value)
{
    atomic_write_f32(&idealLinearSpeed, value);
}

float getIdealAngularSpeed(void)
{
	return atomic_read_f32(&idealAngularSpeed);
}

void setIdealAngularSpeed(float value)
{
    atomic_write_f32(&idealAngularSpeed, value);
}

float getMaxLinearSpeed(void)
{
	return atomic_read_f32(&maxLinearSpeed);
}

void setMaxLinearSpeed(float value)
{
    atomic_write_f32(&maxLinearSpeed, value);
}

void resetMaxLinearSpeed(void)
{
    atomic_write_f32(&maxLinearSpeed, MOUSE_WHEEL_MAX_VEL_MMPS / MILLIMETERS_PER_METER);
}

void updateIdealLinearSpeed(void)
{
	if (idealLinearSpeed < targetLinearSpeed) {
		idealLinearSpeed += getLinearAcceleration() / pidFrequency;
        
		if (idealLinearSpeed > targetLinearSpeed)
			idealLinearSpeed = targetLinearSpeed;
	} else if (idealLinearSpeed > targetLinearSpeed) {
		idealLinearSpeed -= getLinearDeceleration() / pidFrequency;
        
		if (idealLinearSpeed < targetLinearSpeed)
			idealLinearSpeed = targetLinearSpeed;
	}
}

bool sensorIsWallFarFront() {
    uint32_t distance = getRobotDistanceUm(SENSOR_CENTER);
    
    return distance > FAR_FRONT_WALL_DETECTION ? false : true;
}

bool sensorIsWallFront() {
    uint32_t distance = getRobotDistanceUm(SENSOR_CENTER);
    
    return distance > FRONT_WALL_DETECTION ? false : true;
}
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

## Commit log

2024-12-05 Fix UART issues
2024-12-06 Fix UART transmission issue
    [serialComms.c]
2025-01-17 Added schematics and library parts
    SamacSys_party.lbr must be places placed under your "EAGLE/libraries" folder.
    [microm_schem2.sch]
2025-01-17 Add dma and adc code.
2025-01-18 Update schematics and library.
    [microm_schem2.sch]
2025-01-19 Add IMU and LCD, complete wiring and clean up.
    [microm_schem2.sch]
2025-01-19 Fix led resitors.
    [microm_schem2.sch]
2025-01-19 Fix ERC issues and add mounting pads.
    [microm_schem2.sch]
2025-01-20 Add first version of the PCB.
    [microm_schem2.brd, microm_schem2.sch]
2025-01-20 Hide ground airwires.
    [microm_schem2.brd]
2025-01-23 Add changes from meeting today.
    [microm_schem2.brd, microm_schem2.sch]
2025-01-29 Update schematic.
    [microm_schem2.brd, microm_schem2.sch]
2025-01-31 WIP: Trace the airwires
    [microm_schem2.brd, microm_schem2.sch]
2025-02-01 Improve 3.3V routing.
    [microm_schem2.brd, microm_schem2.sch]
2025-02-05 Add most recent board version
    [microm_schem2.brd, microm_schem2.sch]
2025-02-05 Add exported shopping cart of parts
    [Warenkorb_Feb05_0445.xls]
2025-02-05 Fix overlapping uart and sensor routes
    [microm_schem2.brd]
2025-02-05 Move pcb files into subdirectory
    [Warenkorb_Feb05_0445.xls, microm_schem2.brd, microm_schem2.sch]
2025-02-06 Optimizations on pcb, unify via sizes and trace widths.
    [microm_schem2.brd, microm_schem2.sch]
2025-02-08 More wiring optimizations.
    [microm_schem2.brd, microm_schem2.sch]
2025-02-08 Few more optimizations.
    [microm_schem2.brd, microm_schem2.sch]
2025-02-09 Fix DRC issues.
    [microm_schem2.brd]
2025-02-09 Add Beta Layout DRU files.
    [microm_schem2.brd]
2025-02-10 Further refinements.
    [microm_schem2.brd, microm_schem2.sch]
2025-02-10 Minor adjustments.
    [microm_schem2.brd]
2025-02-10 Add GPIO header for remaining pins.
    [microm_schem2.brd, microm_schem2.sch]
2025-02-10 Finalize traces.
    [microm_schem2.brd, microm_schem2.sch]
2025-02-10 Add TUM logo and update values.
    [microm_schem2.brd, microm_schem2.sch]
2025-02-10 Add mouse logo.
    [microm_schem2.brd]
2025-02-11 Add pin descriptions.
    [microm_schem2.brd]
2025-02-11 Fix LED resistors.
    [microm_schem2.brd, microm_schem2.sch]
2025-02-12 Add updated parts list.
    [Warenkorb_Feb05_0445.xls, mouser_cart.xls, rs-online_cart.xls]
2025-02-12 Final fixes.
    [microm_schem2.brd, microm_schem2.sch]
2025-02-27 Adapt source code for pcb pin mapping.
2025-02-28 Add I2C communication code (untested).
2025-03-11 WIP: Add code to setup IMU.
2025-03-13 Add a buffer for async UART and I2C to hold multiple transactions.
2025-03-13 Minor fix in priority.
    [i2c.c, interrupts.h]
2025-03-13 WIP: Read measurements from imu.
2025-03-16 Minor fixes and add code to support RTTTL songs on buzzer.
    [IOconfig.h, dma.c, imu.c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]
2025-03-17 Add first verion of high level maze solving algorithm and PID control
2025-03-17 Fix main IMU bugs.
    [imu.c, imu.h, myTimers.c]
2025-03-18 Add imu gyroscope calibration on startup.
2025-03-20 Add support for timers 4 and 5.
2025-03-25 Add option to init timer in us instead of ms.
2025-03-26 Added implementation for sensors and a first draft for the motors
2025-03-26 Add global timer to track time since startup.
2025-03-26 Change to 16 bit sensor reading and recalibrate sensor
2025-03-26 added scripts and sensor datsa
    [Micromouse_Sensor_Calibration - Tabellenblatt1.csv]
2025-03-26 Fix global timers
2025-03-26 Add motor states turn left, right
2025-03-26 Add functions to change the motors direction individually
2025-03-26 Implemented steering
2025-03-26 Finish missing timer and switch callback implementations, add basic oled
    functions.
    [IOconfig.c, boot.c, i2c.c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]
2025-03-27 Fix timers.
2025-03-27 Fix i2c status.
2025-03-27 Change timer to use for rtttl to be configurable.
2025-03-27 Add PID control
2025-03-27 Change motor standby handling
2025-03-28 WIP: Fix oled interface
    [imu.c, imu.h, oled.c]
2025-03-28 Refactor pwm functions to use integer arithmetic.
2025-03-28 Add pid implementation based on integer arithmetic.
2025-03-30 Add code to calibrate accelerometer.
2025-03-30 WIP: Add odometry tracking.
2025-03-30 WIP: Improve odometry. Add code to turn a certain amount of degrees.
2025-04-15 Add motor encoder changes and fixes.
    [boot.c, imu.c, imu.h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]
2025-04-18 Improve odometry using a complementary filter.
    [acc3_raw.csv, mag3_raw.csv]
2025-04-18 Add velocity and position estimates to odometry.
2025-04-18 fixed visualisation of maze
    [oled.c]
2025-04-18 Add pids to control wheel speeds.
2025-04-21 WIP: Improve encoder velocity estimates and movements.
    [full_acceleration.csv, velocity.csv]
2025-04-23 restructured scripts and img folder
    [full_acceleration.csv, velocity.csv]
2025-04-25 Refactor imu code to support FIFO readings.
    [mag3_raw2.csv]
2025-04-25 Fix max dataset bytes
    [imu.c]
2025-04-26 WIP: Improve movements and odometry
    [mag3_raw_garching.csv]
2025-04-26 WIP: solve the maze and print to oled
2025-04-27 Fix higher level logic
    [mouseController.c]
2025-05-02 WIP: Change movements to a competitive kinematics control.
    [mag3_raw_garching_2.csv]
2025-05-03 WIP: fix issues in ported mouse control code
    [boot.c, constants.h, imu.c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]
2025-05-04 WIP: Try to fix inaccurate distances.
    [boot.c, constants.h, motorEncoders.c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]
2025-05-04 WIP: First version which runs in the maze. Distances are underestimated.
    [full_acceleration.csv]
2025-05-05 WIP: Add better encoder velocity estimat and feedforward term for pid.
    [acceleration_points.csv, exp_fit_params.csv, global_exp_fit_params.csv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]
2025-05-07 Add better plotting code.
    [global_exp_fit_params.csv, segment_vmax_summary.csv]
2025-05-07 Repo cleanup.
    [acceleration_points.csv, enc_velocity_comp.csv, exp_fit_params.csv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]
2025-05-07 Add calibrate source
